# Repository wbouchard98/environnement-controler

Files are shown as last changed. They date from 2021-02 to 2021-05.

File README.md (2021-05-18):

# Projet environnement controlé
Collaborateurs : Simon Jourdenais (Symon4k18) et William Bouchard (wbouchard98)

Ce depôt contient les codes du projet de Serres Domestiques Automatisées, anciennement appelées Environnement Controlé.

Les dossier et fichiers intitulés 'UTest_' sont des tests unitaires.
Le dossier "Trash" contient plusieurs anciens code que nous avons pensés nécessaire, mais après restructuration de notre projet, avons abandonnés. Ces codes ne seront pas aussi bien expliqués et peuvent ne pas toujours fonctionner, mais nous avons décidé de les laisser là comme historique de notre travaille.
Le dossier "Project_Code" contient les codes nécessaires pour faire fonctionner la section logique du projet, tandis que le dossier "Project_EC_GUI" contient les codes nécessaires pour les programmes visuels. Plusieurs version sont disponible montrant l'évolution de notre travaille. Seulement la dernière version est conseillé d'être utilisée.

Le projet suivant sert à prendre des mesures de température, d'humidité et de qualité de l'air, par le biais de différents capteurs et de par la suite
réguler l'environnement.

Voici la liste de matériel utilisé pour le projet:
	1) RaspberryPi 4
	2) PCB "Bloc de capteurs" *
	3) PCB "Bloc de contrôle" *
	4) DS18B20 x2
	5) CSS811
	6) SEN0227
	7) Écran LCD tactile 7 pouces
	8) Bloc d'alimentation d'ordinateur 450 watts

	*Les détails des PCB seront montré plus loin.

Pour que le RaspberryPi fonctionne pour ce projet, voici les étapes que nous avons effectué:

RPIlogo 
# Étapes de l’installation de l’image du Raspberry Pi 

1)	Allez chercher une image de Raspberry Pi Buster Desktop 
2)	”Flash” une carte SD d’au moins 8Go avec cette image. Nous avons utilisé Balena Etcher pour cette étape.
3)	Faire la configuration du Raspberry Pi lors de son premier démarrage. Lorsqu’il vous est demandé de redémarrer le Raspberry Pi, redémarrer le.
4)	Maintenant, il faut activer les interfaces dont on aura besoin. Ouvrez un terminal, et tapez la commande : sudo raspi-config
5)	Une fois la fenêtre de configuration ouverte sélectionner l’index 5(Interfacing Options).
6)	Activer ‘’SSH’’, ‘’VNC’’, ‘’I2C’’ et ‘’1-Wire’’. Il faut aussi activer le ‘’Serial’’. Cependant lorsqu’il va être demandé s’il est désiré que le ‘’login shell’’ soit accessible depuis le serial, faire non, et lorsque l’usager est demandé de vouloir activer le ‘’Serial port hardware’’ faire oui.
7)	Redémarrez le Raspberry Pi pour effectuer les changements.
8)	Maintenant, il faut se connecter au serveur de temps pour pouvoir automatiquement mettre à jour le temps du Raspberry Pi. Ouvrez le fichier /etc/systemd/timesyncd.conf .
9)	Modifiez les lignes ‘’NTP’’ et ‘’FallbackNTP’’ pour que leur valeur sois : time.apple.com .
10)	Effectuez un : sudo systemctl restart systemd-timesync.service .
11)	Effectuer par la suite : sudo systemctl daemon-reload .
12)	Maintenant faire les ‘’update’’ et ‘’upgrade’’.
13)	Si vous utilisez un écran de petite taille, comme un écran 7" comme nous, nous vous recommandons de changer la résolution de l'écran. Pour ce faire, cliquer le logo Raspberry dans le haut de l'écran, puis aller sur "Preferences" et "Raspberry Pi Configuration". Aller dans l'onglet "Display" et puis "Set Resolution...". Nous utilisons "DMT mode 9 800x600 60Hz 4:3".

Une fois le RaspberryPi bien configuré, il faut ajouter les bonnes librairies pythons dans le RaspberryPi pour que les codes puissent bien fonctionner.

Voici les démarches à suivre pour l'installation de ces librairies:

Pyhton
# Étapes pour l’installation des librairies Python

1) Premièrement, il faut s’assurer que Pyhton3 soit bien installé : sudo apt-get install python3 .
2) Une fois installé, il faut pouvoir accéder au I/O du Raspberry Pi. La librairie suivante va faire ce travail : sudo pip3 install RPI.GPIO
3) Pour pouvoir lire les données du capteur SEN0227 qui va lire la température de l’environnement dans lequel le Raspberry Pi se situe (et non l’environnement que l’on souhaite contrôler) : sudo pip3 install sht20 .
4) Maintenant, pour être capable de faire les communications MQTT, il nous faut un "Broker MQTT" : sudo apt-get install mosquitto : et : sudo apt-get install mosquitto-clients .
5) Une fois le "Broker" installé, il nous faut la librairie pour accéder à ce "Broker" : sudo pip3 install paho-mqtt .
6) Maintenant, il faut que notre "GUI" puisse accéder aux librairies PYQT5 : sudo apt-get install qt5-default pyqt5-dev pyqt5-dev-tools
7) Pour contrôler la plupart des éléments de l’environnement, l’utilisation d’un PID est importante. La librairie suivante va nous permettre d’utiliser des PID : sudo pip3 install simple-pid .

Maintenant il est temps d'ajouter les librairies à l'IDE Arduino:

Arduino
# Étape pour l’installation des librairies Arduino

1) Adafruit_CCS811: Pour l'ajouter à l'IDE Arduino, ouvrir l'IDE Arduino, cliquer sur l'onglet "Croquis". Aller par la suite sur "Inclure une bibliothèque" et ensuite "Gérer les bibliothèques". Taper "CCS" dans la barre de recherche et une librairie du nom de "Adafruit CSS811 Library par Adafruit" devrait être disponible. Cliquer sur "Installer".  

2) DFRobot_SHT20: Pour ajouter cette librairie, visiter DFRobot/DFRobot_SHT20 (github.com) . Télécharger le repositary avec le bouton vert avec la flèche. Une fois télécharger mettre le dossier "DFRobot_SHT20-master" dans le dossier "C:\Program Files (x86)\Arduino\libraries". 

3) OneWire: Suivre les étapes pour le Adafruit_CCS811, mais taper "Onewire" dans la barre de recherche. Dans le "ComboBox" "Sujet" sélectionner "Communication". Une librairie du nom de "OneWire" devrait être disponible. Installer celle-ci. 

4) DallasTemperature: Suivre les étapes pour le Adafruit_CCS811, mais tapper "Dallas" dans la barre de recherche. Une librairie du nom de "DallasTemperature" devrait être        disponible. Installer celle-ci. 

## Explication des PCB

Notre projet contient deux PCB. L'un d'entre eux sert à la lecture des capteurs, et l'autre sert à contrôler les diverts éléments de contrôle.
### PCB bloc de capteurs

Pour lire l'état actuel de la chambre, nous avons créé un PCB qui relie plusieurs capteurs(DS18B20, SEN0227, CCS811) à un ATmega328p-AU. Les informations des capteurs sont ensuites transmises au RaspberryPi.
#### Transmission des informations
Nous utilisons la prise USB-mini pour transmettre les informations des capteurs vers le RaspberryPi. Ce même connecteur peut être utilisé pour le transfert du code .ino/.c. Nous avons aussi mis des traces pour un connecteur pour le module bluetooth HM-10.
Pour changer le mode entre Bluetooth et USB, il suffit de changer la position du cavalier JP201 et JP203 (position 1-2 Bluetooth, 2-3 USB). 
Dans notre projet nous utilisons pas le module Bluetooth, alors aucun code n'a été fait pour son utilisation, mais son ajout peut être possible grâce au PCB.
#### Alimentation
L'alimentation de ce PCB vient du câble USB, mais si on désire utiliser le module Bluetooth, alors un connecteur(J202) permet de connecter une batterie Li-po de 5V pour alimenter le montage de façon indépendante au RaspberryPi.
Comme mentionné plus tôt, nous utilisons la communication USB, alors l'alimentation provenant de batterie Li-po n'a pas été testé.
#### Communication des capteurs
##### DS18B20
Le capteur de température DS18B20 communique avec le ATmega en protocole 1-wire. La plaque contient une empreinte pour placer directement un DS18B20 en format TO-92, et un connecteur permet de pouvoir aussi utiliser un DS18B20.
##### SEN0227
Le capteur de température/humidité SEN0227 communique en I2C avec le ATmega. La plaque contient une empreinte pour placer directement un SHT-20, et un connecteur permet de pouvoir aussi utiliser un SEN0227.
##### CCS811
Le capteur de qualité de l'air CCS811 communique en I2C avec le ATmega. La plaque contient les empreintes pour placer directement CCS811 et les composants requis pour son fonctionement, et un connecteur permet de pouvoir aussi utiliser un CCS811 de Keyestudio.
La trace JP301 permet de changer l'adresse du CCS811.
##### SGP30
Le capteur de qualité de l'air SGP30 communique en I2C avec le Atmega. La plaque contient une empreinte pour placer directement un SGP30, et un connecteur permet de pouvoir aussi utiliser un "board" SGP30 de Adafruit.
Dans notre projet nous utilisons pas le SGP30, alors aucun code dans notre conteneur Github sera fait avec la considération de son utilisation, mais il sera possible de modifier le code pour l'inclure s'il est désiré.

### PCB de contrôle

Ce PCB sert à transformer les PWM du RaspberryPi, pour qu'ils soient capable de contrôler les éléments de contrôle(Lumière, ventillation, chauffage, humidificateur).

#### Connection au RaspberryPi
Le RaspberryPi se connecte au PCB par l'entremise d'un câble plat 40 pins.
#### Ventillation
La ventillation est contrôllé par le GPIO-27 du RaspberryPi. Le signal du GPIO-27 est ensuite transformer en 120 VAC par un CPC1966B pour faire fonctionner le système de ventillation.

#### Élément chauffant
Même méthode que pour la ventillation, mais le GPIO-17 est utilisé.

#### Lumière
Même principle que la ventillation, mais le GPIO-06 est utilisé.

#### Déshumidificateur
Même principle que la ventillation, mais le GPIO-22 est utilisé. On a pas intégré le déshumidificateur à notre projet, alors notre code ne contient pas son activation, mais il est possible d'ajouter son activation si désiré.

#### Humidificateur
L'humidificateur est contrôlé par le GPIO-05 du RaspberryPi. Un CPC1907B transforme le signal du RaspberryPi en signal 24V.

#### LED 100W
Une LED de 100W peut être connecté au PCB pour utiliser au lieu du panneau de lumière. Cette lumière sera contrôlé par le GPIO-13 du RaspberryPi. Un transitor permet de faire circuler le courant pour allumer la LED.

#### Ventillation du boitier
Un ventillateur à l'intérieur du boitier permet de refroidir la température de celui-ci. Ce ventillateur est contrôllé par un PWM de la pin GPIO-12 du RaspberryPi. Un transitor permet de conduire le courant à partir du 12V.

#### Ventillateur de la LED 100W
Un ventillateur qui permet de refroidir la LED de 100W. Ce ventillateur est "driver" par un transitor contrôlé par la pin GPIO-18 du RaspberryPi.

#### Connecteur 12V supplémentaire
On ajouté ce connecteur pour pouvoir ajouter d'autre élément fonctionnant sur du 12V. Comme par exemple une pompe à eau pour arroser la terre ou un ventillaeur supplémentaire. Ce connecteur sera contrôler par la pin GPIO-19 du RaspberryPi.

## Utilisation de l'interface graphique
L'interface graphique se compose de deux sections: un menu ancré sur la gauche de l'écran et l'affichage principale qui occupe le restant. Voir figure ci-dessus.

SecGUI

Le menu nous permet de naviguer entre 4 modes de GUI différents. Le premier est le mode monitorage, le deuxième est le mode consigne, le troisième est le mode paramètre et finalement le dernier est le mode administrateur.

### Mode Monitorage
Le mode monitorage est bien simple; il affiche les valeurs reçues. Les valeurs sont la température, l'humidité, la concentration de C02 et la quantité de matière organique dans l'air. Voir la figure ci-dessus pour exemple de l'affichage en mode monitorage.

MonGUI

### Mode Consigne
Le mode consigne permet à l'usager d'accomplir plusieurs tâches. Premièrement, une section de l'affichage est réservé à afficher les valeurs de consignes courantes. Une autre section sert à modifier manuellement les valeurs des consignes courantes. Les valeurs à l'écran dans la section de l'affichage des consignes vont changer avec les modifications effectué. L'autre section sert à choisir ou enregistrer des valeurs de consignes. Ces valeurs sont alors réutilisables si l'usager souhaite les utiliser plus tard, ou si le système est mis hors tension. Voir la figure ci-dessus pour un visuel du GUI en mode consigne. Il est aussi possible d'ouvrir une autre fenêtre qui va permettre le contrôle des lumières.

ConGUI

#### Mode éclairage
Appelé à partir de la fenêtre consigne, permet de configurer un cycle d'activation et de désactivation des lumières.

ConGUI

### Mode Paramètre
Le mode paramètre nous permet de se connecter à la base de données ThingSpeak, de se connecter à un réseau Wi-Fi et à voir des informations utiles pour l'usgaer. Pour pouvoir entrer les informations requises de Thingspeak et du Wi-Fi, un clavier sera nécessaire. Simplement le brancher dans un port USB du RaspberryPi. L'iamge ci-dessous nous permet de voir un exemple de la fenêtre paramètre.

ParaGUI

### Mode Administrateur
Le mode Administarteur permet de contrôler manuellement les éléments de contrôle. Cette fenêtre est très utile pour vérifier le fonctionnment de son matériel. Des "sliders" servent à ajuster le PWM des éléments et ainsi dicter leur intensité de fonctionnment. Voir la figure ci-dessus pour un apperçu.

AdminGUI

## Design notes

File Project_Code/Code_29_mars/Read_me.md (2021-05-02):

# Fonctionnement des codes du projet

Les programmes dans ce dossier sont les programmes les plus à jours à date du 29 Mars 2021. Ces programmes peuvent fonctioner à l'aide du PCB "Bloc de capteur" ou à l'aide d'un Arduino Nano
avec les capteurs relié au bonne pattes de communication.

Pour pouvoir avoir les librairies nécessaire et que la configuration des systèmes soient correct, veuillez vous référer au Read_me.md principal du répertoire GitHub.

## P_p_3.py

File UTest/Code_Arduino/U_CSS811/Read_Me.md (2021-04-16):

Test unitaire pour le fonctionnement du capteur CCS811. 
IMPORTANT!!!!!! Le capteur de CO2 nécessite 48H de marche, après chaque mise a l'arrêt avant de donner des donées précises.
Pour vérifier son fonctionnement, veuillez le connecter au RaspberryPi et mettre en marche le code Userial_read_from_arduino.py dans le RaspberryPi.

Matériel:
	ARDUINO NANO
	CONVERTISSEUR 5v -> 3.3V
	RASPBERRY PI 3B
	CAPTEUR CCS811

Connexion:
	Pour que le test du capteur CCS811 fonctionne, les connexions suivantes doivent être éffectuées:

		ARDUINO NANO -> CC811:
			GND  ->  GND
			5V   ->  VCC
			A4   ->  SDA
			A5   ->  SCL
			GND  ->  WAKE
			N.C. ->  RST, INT

		ARDUINO NANO -> CONVERTISSEUR(HIGH/LOW) -> RASPBERRY PI 3B
			GND  ->  	GND <-> GND    	<-  GND		#Connection du GND entre le RPi et le ARDUINO direct + connexion au GND du convertisseur
			5V   ->		HV  :  LV       <-  3.3V
			RX0  ->         HV3 :  LV3      <-  TX(Pin8)
			TX1  ->         HV1 :  LV1      <-  RX(Pin10)

Prérequis:
	Programme Arduino:
		Pour le bon fonctionnement du programme Arduino, la librairie "Adafruit_CCS811" est nécessaire.
		Pour l'installer dans l'IDE ARDUINO:
			1) Ouvrir l'IDE ARDUINO
			2) Cliquer sur 'Croquis' dans la barre d'outils.
			3) Sélectionner 'Inclure une bibliothèque', puis 'Gérer les bibliothèque'.
			4) Dans la nouvelle fenêtre, assurez-vous que 'Type' et 'Sujet' sois a 'Tout'.
			5) Dans le filtre de recherche, tapez 'CCS811' et une librairie Adafruit devrait être disponible. Cliquer sur 'Installer'.
			6) Redémarrez l'IDE.

Transfert du code ARDUINO (CCS881.c):
	1) Assurez-vous que les options de téleversement soient les bonnes. (Carte: "Arduino Duemilanove", Processeur: "ATmega328p", PORT: Choisir le bon, Programmateur: "AVR ISP")
	2) Avant de téléverser le code, débrancher les connections rx/tx du ARDUINO NANO pour que le port série communique bien avec celui de l'ordinateur.
	3) Une fois le code téléverser, refaire les connections RX/TX.

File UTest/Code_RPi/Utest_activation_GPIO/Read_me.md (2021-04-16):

Test unitaire pour tester la librairie RPi.GPIO.

Le test sert à savoir si les librairies de base python ont bien été installées. (Pour installer python: sudo apt-get install pyhton3)

Le script met un état haut au GPIO-16 du Pi pendant 5 secondes.

Matériel:

	RASPBERRY PI 3B

PRÉALLABLES :

	Vous deves avoir la librairie RPi.GPIO. Pour l'installée, entrer la commande suivante dans un terminal: sudo pip3 install RPi.GPIO

EXÉCUTION : 

	Excécuter le programme et vérifier l'état du GPIO-16 du RaspberryPi. Si un état haut de 5 secondes est détecté, alors la librairie devrait être OK.

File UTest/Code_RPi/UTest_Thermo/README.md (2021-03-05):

README pour le fichier UTest_Thermo_DS18B20.py

BRANCHEMENT :

Le thermomêtre DS18B20 doit être alimenté avec 5 volts ou 3.3 Volts et le brancher sur l'entrée IO4, qui corresponds à la pin 1-Wire.
Ne pas oublier d'ajouter une pull-up de 4.7k sur le one-wire

PRÉALLABLES :

Pour exécuter ce programme de test unitaire, vous devez préallablement configurer votre Raspberry Pi. 
Exécuter la commande 'sudo raspi-config', puis dans la section 'Interfaces', activez l'interface '1-Wire'.

De plus, exécutez la ligne 'sudo pip3 install w1thermsensor' pour installer la librairie du thermomêtre dans le dossier contenant ce fichier.

EXÉCUTION : 

Une fois fait, ouvrez un terminal dans le dossier UTest_Thermo et exécutez la ligne 'python UTest_Thermo_DS18B20.py'.
La valeur lue du thermomêtre sera alors affichée dans le terminal si tout est bien branché et que les préallables on été faits et/ou installés.

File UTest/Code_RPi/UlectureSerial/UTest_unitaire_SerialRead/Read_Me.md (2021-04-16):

Test unitaire pour la lecture du port série.
Le faire marcher avec le code CCS811.c du Arduino Nano permet de vérifier si la communication série est bien établie et si le capteur CCS811 est fonctionnel.
Permet aussi de s'assurer que la configuration du port série du Raspberry Pi à bien été faite.

Matériel:
	ARDUINO NANO
	CONVERTISSEUR 5v -> 3.3V
	RASPBERRY PI 3B

Connexion:

		ARDUINO NANO -> CONVERTISSEUR(HIGH/LOW) -> RASPBERRY PI 3B
			GND  ->  	GND <-> GND    	<-  GND		#Connection du GND entre le RPi et le ARDUINO direct + connexion au GND du convertisseur
			5V   ->		HV  :  LV       <-  3.3V
			RX0  ->         HV3 :  LV3      <-  TX(Pin8)
			TX1  ->         HV1 :  LV1      <-  RX(Pin10)

Le programme suivant devrait lire ce qui est sur le port série et afficher le résultat en console.

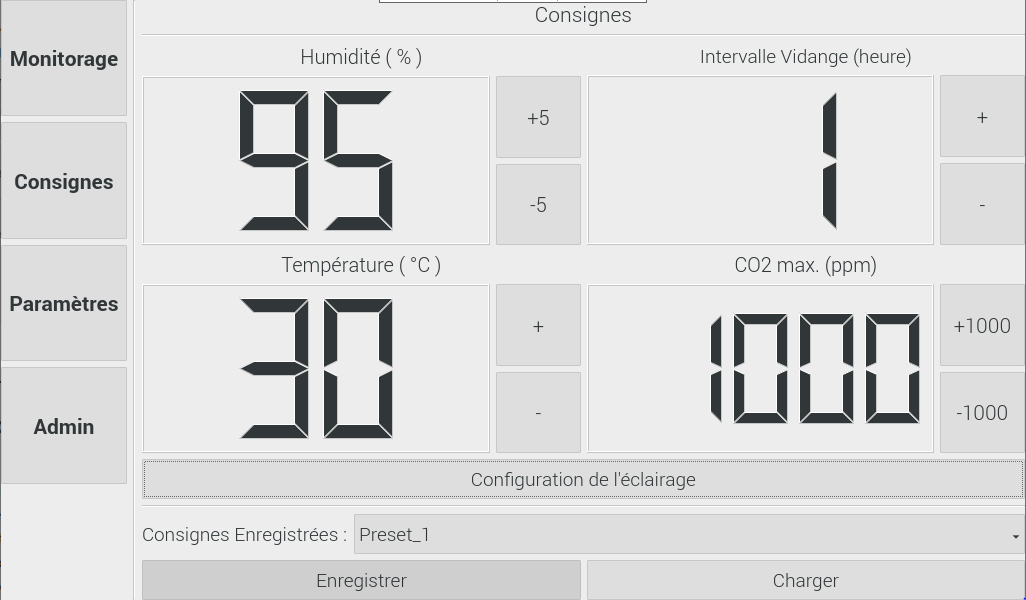
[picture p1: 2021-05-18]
Trash/CaptureControl.PNG

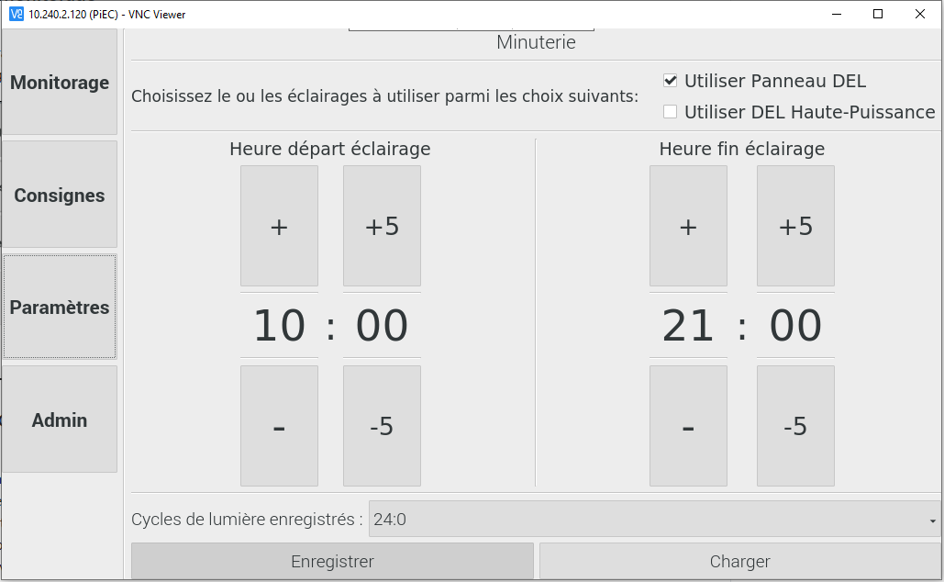
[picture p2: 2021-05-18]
Trash/CaptureControlTime.PNG

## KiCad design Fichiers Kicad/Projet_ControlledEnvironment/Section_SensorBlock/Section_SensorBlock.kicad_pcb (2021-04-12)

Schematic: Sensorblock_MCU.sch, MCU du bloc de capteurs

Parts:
C201, C202, C205, C206, C208: 0.1 uF; C_0805_2012Metric
C203, C204: 18 pF; C_0805_2012Metric
C207: 1 uF; C_0805_2012Metric
C209: 10 uF; C_0805_2012Metric
D201: D_Schottky; D_0805_2012Metric
D202: LED_RED_TX; LED_0805_2012Metric
D203: LED_BLUE_RX; LED_0805_2012Metric
D205: LED_YLW_USR; LED_0805_2012Metric
D206: LED_RED; LED_0805_2012Metric
D207, D208: LED_YLW; LED_0805_2012Metric
D209, D210: LED_GRN; LED_0805_2012Metric
ICSP201: Conn_02x03; PinHeader_2x03_P2.54mm_Vertical
J201: USB_B_Mini; USB_Mini-B_Lumberg_2486_01_Horizontal
J202: Conn_01x02_Female; PinSocket_1x02_P2.54mm_Vertical
J203: Sense_Batt; PinSocket_1x01_P2.54mm_Vertical
JP201, JP203: Jumper_NC_Dual; PinHeader_1x03_P2.54mm_Vertical
R201: 90k; R_0805_2012Metric
R202, R203: 10k; R_0805_2012Metric
R204, R205, R208, R209, R210, R211, R212, R213: 330; R_0805_2012Metric
R206: 4.7k; R_0805_2012Metric
SW201: Reset; SW_SPST_CK_RS282G05A3
SW202: SW_Push; SW_PUSH-12mm_Wuerth-430476085716
U201: ATmega328P-AU; TQFP-32_7x7mm_P0.8mm
U202: FT232RL; SSOP-28_5.3x10.2mm_P0.65mm
U203: HM10; PinHeader_1x04_P2.54mm_Vertical
U204: AP2210-3.3; SOT-23
Y201: 16 MHz; Crystal_SMD_5032-2Pin_5.0x3.2mm

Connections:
+3V3: C208.1, C209.1, U202.17, U204.2; also elsewhere on the board
+5V: C201.2, C202.2, C205.2, C207.1, D201.1, ICSP201.2, J202.1, R203.1, R204.2, R205.1, SW202.1, U201.4 (VCC), U201.6 (VCC), U201.18 (AVCC), U202.4, U202.20, U203.4, U204.3; also elsewhere on the board
/Sensorblock MCU sheet/BTN_In: R206.1, SW202.2, U201.23 (PC0)
/Sensorblock MCU sheet/BT_RX: JP201.1, U203.1
/Sensorblock MCU sheet/BT_TX: JP203.1, U203.2
/Sensorblock MCU sheet/DTR: C206.1, U202.2
/Sensorblock MCU sheet/LED_Meter_1: D206.2, U201.1 (PD3)
/Sensorblock MCU sheet/LED_Meter_2: D207.2, U201.2 (PD4)
/Sensorblock MCU sheet/LED_Meter_3: D208.2, U201.9 (PD5)
/Sensorblock MCU sheet/LED_Meter_4: D209.2, U201.10 (PD6)
/Sensorblock MCU sheet/LED_Meter_5: D210.2, U201.11 (PD7)
/Sensorblock MCU sheet/PB2-SS: U201.14 (PB2)
/Sensorblock MCU sheet/PB3-MOSI: ICSP201.4, U201.15 (PB3)
/Sensorblock MCU sheet/PB4-MISO: ICSP201.1, U201.16 (PB4)
/Sensorblock MCU sheet/PB5-SCK: D205.2, ICSP201.3, U201.17 (PB5)
/Sensorblock MCU sheet/PC6-RST: C206.2, ICSP201.5, R203.2, SW201.1, U201.29 (~RESET~/PC6)
/Sensorblock MCU sheet/RX_ARD: JP203.2, U201.30 (PD0)
/Sensorblock MCU sheet/TX_ARD: JP201.2, U201.31 (PD1)
/Sensorblock MCU sheet/USB_RX: JP201.3, U202.5
/Sensorblock MCU sheet/USB_TX: JP203.3, U202.1
AT_1Wire: U201.32 (PD2); also elsewhere on the board
AT_SCL: U201.28 (PC5); also elsewhere on the board
AT_SDA: U201.27 (PC4); also elsewhere on the board
unnamed: C203.2, U201.7 (XTAL1/PB6), Y201.1
unnamed: C204.2, U201.8 (XTAL2/PB7), Y201.2
unnamed: D201.2, J201.1 (VBUS)
unnamed: D202.1, U202.23
unnamed: D202.2, R204.1
unnamed: D203.1, U202.22
unnamed: D203.2, R205.2
unnamed: D205.1, R208.1
unnamed: D206.1, R209.1
unnamed: D207.1, R210.1
unnamed: D208.1, R211.1
unnamed: D209.1, R212.1
unnamed: D210.1, R213.1
unnamed: J201.2 (D-), U202.16
unnamed: J201.3 (D+), U202.15
unnamed: J203.1, R201.1
unnamed: R201.2, R202.1, U201.24 (PC1)

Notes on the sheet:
Pour entrée 5V de batterie LiPo
Si le module Bluetooth est utilisé, ne pas oublier de changer les cavaliers de position!
Régulateur 3.3 pour les capteurs - Le FTDI ne peux sourcer plus de 50 mA

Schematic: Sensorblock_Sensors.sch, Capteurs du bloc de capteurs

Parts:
C301, C302: 0.1 uF; C_0805_2012Metric
J301: Conn_OLED_Screen; PinSocket_1x04_P2.54mm_Vertical
J302: Conn_01x04; PinSocket_1x04_P2.54mm_Vertical
J303: Conn_QT_CCS; PinSocket_1x04_P2.54mm_Vertical
J304: Conn_Keyes_CCS; PinSocket_1x07_P2.54mm_Vertical
J305: Conn_QT_SGP30; PinSocket_1x04_P2.54mm_Vertical
J306: Conn_01x03; PinSocket_1x03_P2.54mm_Vertical
JP301: Jumper_Address_I2C; SolderJumper-2_P1.3mm_Open_TrianglePad1.0x1.5mm
Q301, Q302, Q303: BSS138; SOT-23
R301, R302, R303, R304, R305, R306, R307, R309: 10k; R_0805_2012Metric
R311: 4.7 Ohms; R_0603_1608Metric
R312: 100k; R_0805_2012Metric
TH301: 10k; R_0402_1005Metric
U301: CCS811; AMS_LGA-10-1EP_2.7x4mm_P0.6mm
U302: DS18B20; TO-92_Inline
U303: SHT2x; DFN-6-1EP_3x3mm_P1mm_EP1.5x2.4mm
U304: SGP30; DFN-7

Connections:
+3V3: C301.1, J301.3, J302.2, J303.2, J304.2, J305.2, J306.1, JP301.1, Q301.1, Q302.1, Q303.1, R304.2, R305.2, R306.2, R309.2, R311.1, R312.2, U301.2, U301.6, U302.3 (VDD), U303.5, U304.5; also elsewhere on the board
+5V: R301.2, R302.2, R303.2; also elsewhere on the board
/Sensorblock sensor sheet/1Wire_3V3: J306.2, Q303.2, R306.1, U302.2 (DQ)
/Sensorblock sensor sheet/CO2_!Int: U301.3
/Sensorblock sensor sheet/SCL_3V3: J301.2, J302.4, J303.4, J304.4, J305.4, Q301.2, R304.1, U301.10, U303.6, U304.6
/Sensorblock sensor sheet/SDA_3V3: J301.1, J302.3, J303.3, J304.3, J305.3, Q302.2, R305.1, U301.9, U303.1, U304.3
AT_1Wire: Q303.3, R303.1; also elsewhere on the board
AT_SCL: Q301.3, R301.1; also elsewhere on the board
AT_SDA: Q302.3, R302.1; also elsewhere on the board
unnamed: C302.2, R311.2, U304.1
unnamed: JP301.2, R307.2, U301.1
unnamed: R312.1, TH301.2, U301.8
unnamed: TH301.1, U301.4, U301.5

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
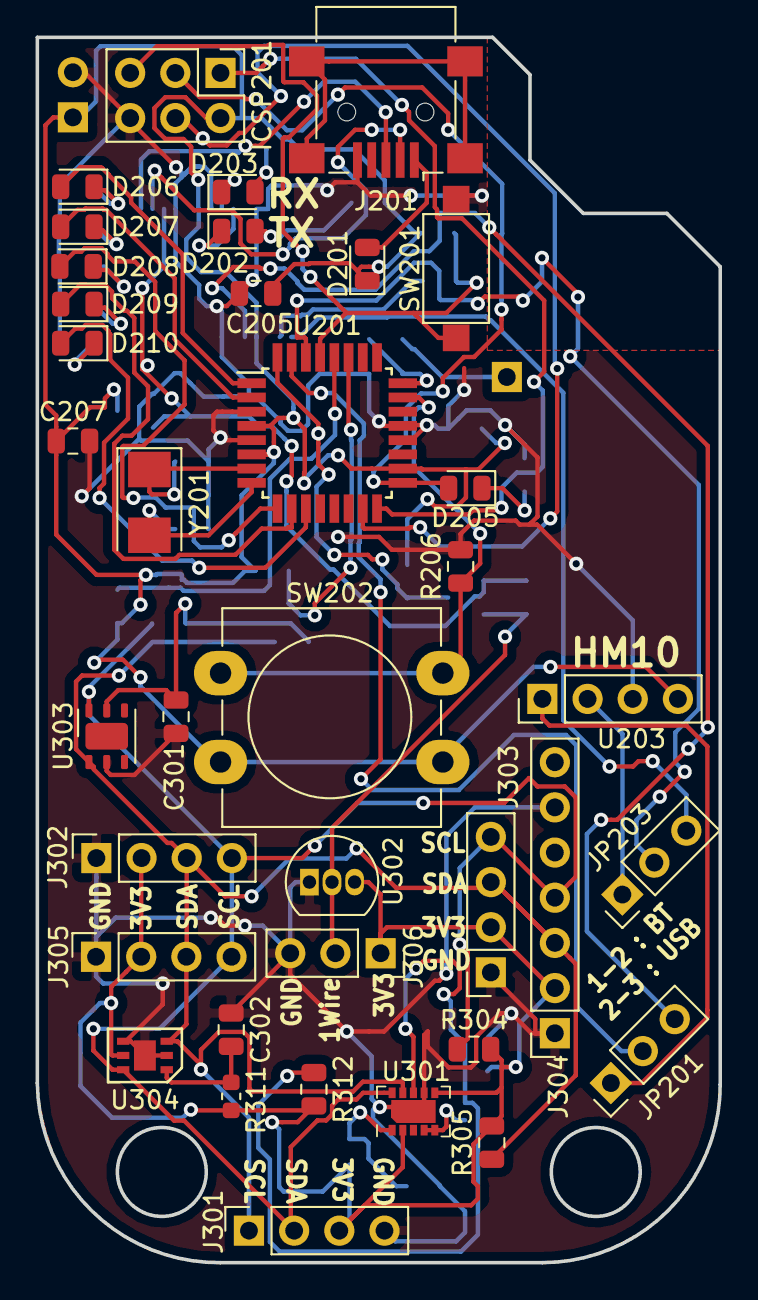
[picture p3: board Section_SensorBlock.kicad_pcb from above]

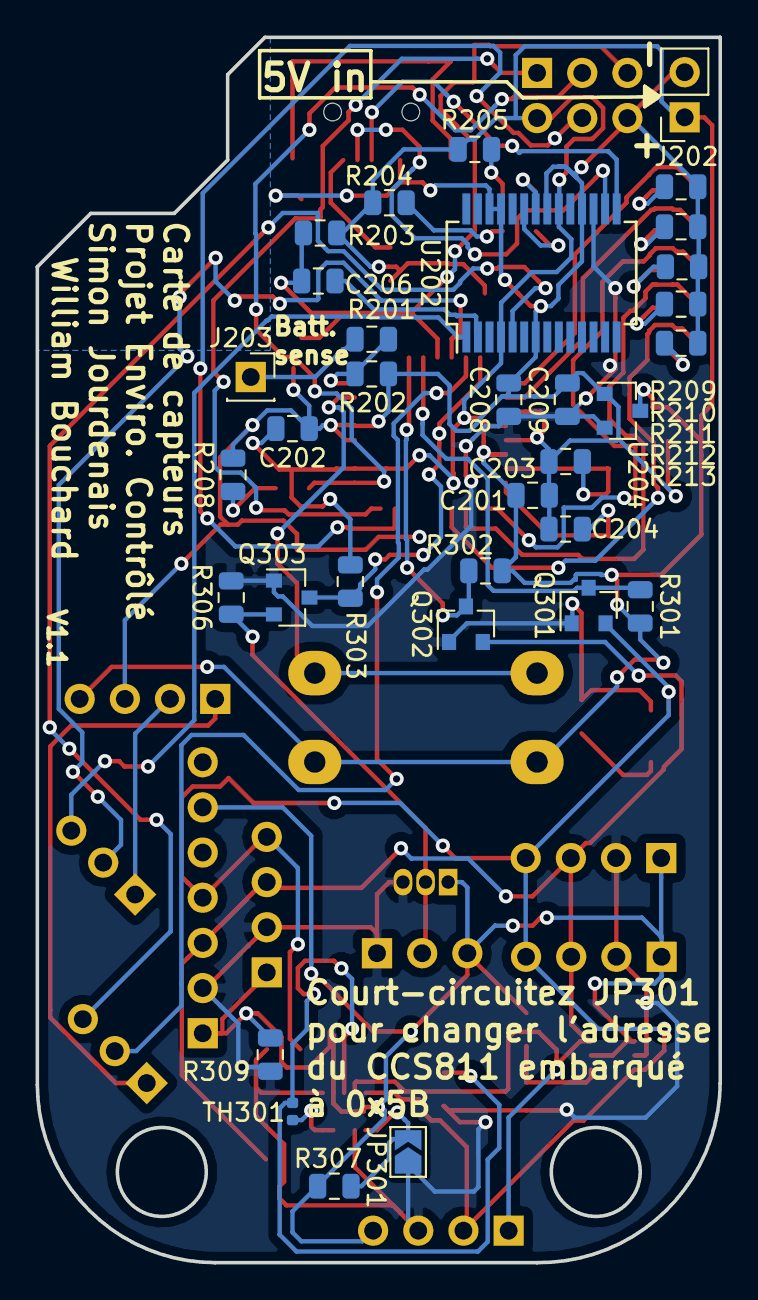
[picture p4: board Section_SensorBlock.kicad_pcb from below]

Board: 2 copper layers, 38.4 x 68.9 mm, 70 parts (33 on the bottom side), 47 nets.

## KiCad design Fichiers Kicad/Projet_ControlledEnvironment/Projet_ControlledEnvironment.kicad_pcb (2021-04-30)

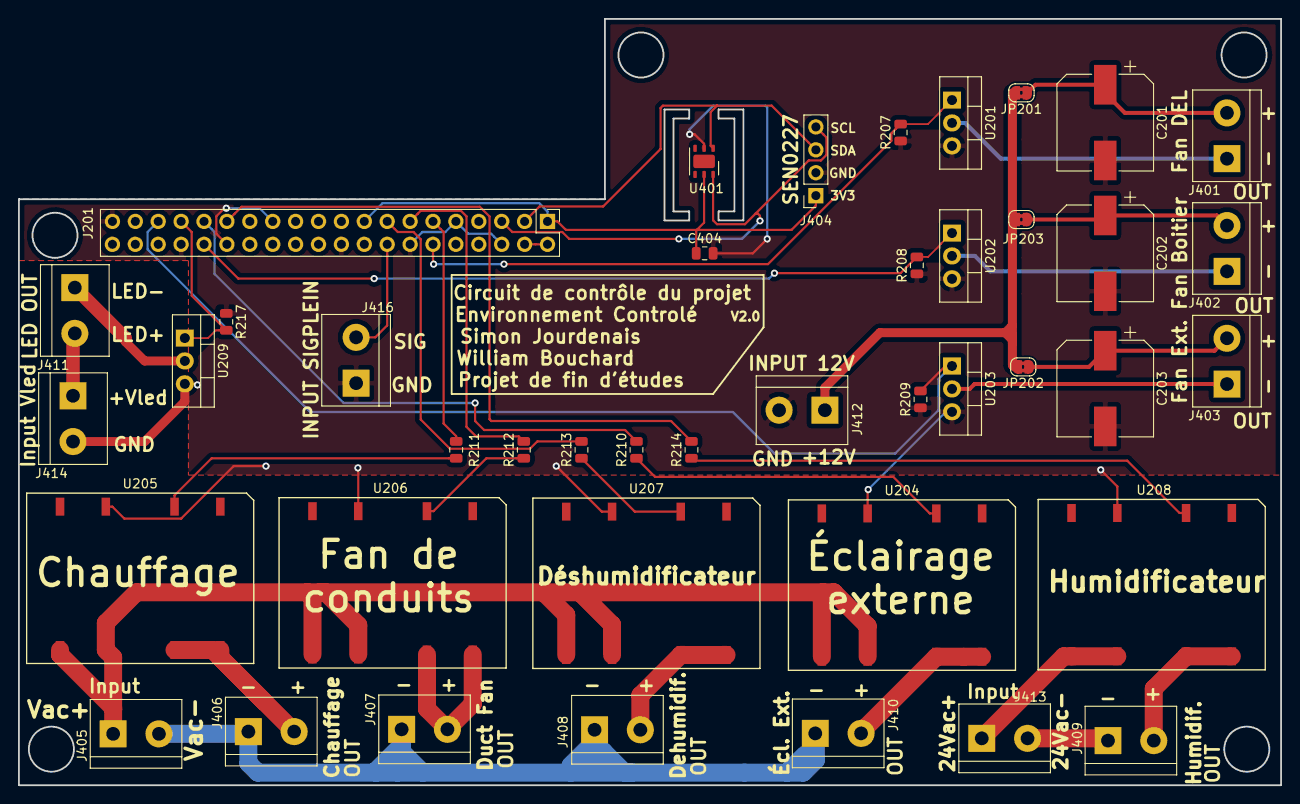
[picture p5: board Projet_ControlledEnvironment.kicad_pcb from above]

Board: 2 copper layers, 140.0 x 85.0 mm, 42 parts (0 on the bottom side), 38 nets.

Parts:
C201, C202, C203: 470 uF; CP_Elec_10x10.5
C404: 0.1 uF; C_0805_2012Metric
J201: Pi 40-Pin Connector; PinHeader_2x20_P2.54mm_Vertical
J401, J402, J403, J405, J406, J407, J408, J409, J410, J411, J412, J413, J414, J416: Conn_01x02; TerminalBlock_bornier-2_P5.08mm
J404: Conn_01x04; PinSocket_1x04_P2.54mm_Vertical
JP201, JP202, JP203: SolderJumper_2_Bridged; SolderJumper-2_P1.3mm_Bridged2Bar_RoundedPad1.0x1.5mm
R207, R208, R209, R217: 10k; R_0805_2012Metric
R210, R211, R212, R213, R214: 420; R_0805_2012Metric
U201, U202, U203, U209: FQP30N06L; TO-220-3_Vertical
U204, U205, U206, U207: CPC1966B; PSOIC-8
U208: CPC1907B; PSOIC-8
U401: SHT2x; DFN-6-1EP_3x3mm_P1mm_EP1.5x2.4mm

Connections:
24VAC+: J413.1, U208.5, U208.6
24VAC-: J409.1, J413.2
100W_LED+: J411.2, J414.1
100W_LED-: J411.1, U209.2
+3V3: C404.1, J201.1, J201.17, J404.1, U401.5
+5V: J201.2, J201.4
+12V: J412.1, JP201.2, JP202.2, JP203.2
/Mainblock Core/GPIO5: J201.29, R214.2
/Mainblock Core/GPIO6: J201.31, R210.2
/Mainblock Core/GPIO12: J201.32, R208.2, U202.1
/Mainblock Core/GPIO13: J201.33, R217.2, U209.1
/Mainblock Core/GPIO17: J201.11, R211.2
/Mainblock Core/GPIO18: J201.12, R207.2, U201.1
/Mainblock Core/GPIO19: J201.35, R209.2, U203.1
/Mainblock Core/GPIO22: J201.15, R213.2
/Mainblock Core/GPIO27: J201.13, R212.2
BOITIER_FAN_IN: C202.1, J402.2, JP203.1
BOITIER_FAN_OUT: J402.1, U202.2
Dehumidificateur: J408.2, U207.7, U207.8
DuctFan: J407.2, U206.7, U206.8
EXT_OPT_FAN_IN: C203.1, J403.2, JP202.1
EXT_OPT_FAN_OUT: J403.1, U203.2
Ext_Light: J410.2, U204.7, U204.8
GND: C201.2, C202.2, C203.2, C404.2, J201.6, J201.9, J201.14, J201.20, J201.25, J201.30, J201.34, J201.39, J404.2, J412.2, J414.2, J416.1, R207.1, R208.1, R209.1, R217.1, U201.3, U202.3, U203.3, U204.3, U205.3, U206.3, U207.3, U208.3, U209.3, U401.2
GPIO23_SIGPLEIN: J201.16, J416.2
Heater: J406.2, U205.7, U205.8
Humidificateur: J409.2, U208.7, U208.8
LED_FAN_IN: C201.1, J401.2, JP201.1
LED_FAN_OUT: J401.1, U201.2
unnamed: R210.1, U204.2
unnamed: R211.1, U205.2
unnamed: R212.1, U206.2
unnamed: R213.1, U207.2
unnamed: R214.1, U208.2
SCL_PI: J201.5, J404.4, U401.6
SDA_PI: J201.3, J404.3, U401.1
VAC+: J405.1, U204.5, U204.6, U205.5, U205.6, U206.5, U206.6, U207.5, U207.6
VAC-: J405.2, J406.1, J407.1, J408.1, J410.1

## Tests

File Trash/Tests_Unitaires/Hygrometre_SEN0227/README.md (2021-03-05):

README pour le fichier UTest_Hygro_SEN0227.py

BRANCHEMENT :

L'hygromètre SEN0227 doit être alimenté avec 3.3 Volts, son 'SDA' branché dans l'entrée IO2 et le 'SCL' dans l'entrée IO3.

PRÉALLABLES :

Pour executer ce programme de test unitaire, vous devez préallablement configurer votre Raspberry Pi. 
Éxecuter la commande 'sudo raspi-config', puis dans la section 'Interfaces', activez l'interface 'I2C'.

De plus, executez la ligne 'sudo pip3 install sht20' pour installer la librairie du capteur.

EXÉCUTION : 

Une fois fait, ouvrez un terminal dans le dossier UTest_Hygro et exécutez la ligne 'python UTest_Hygro_SEN0227.py'.
Les valeurs lues du capteur seront alors affichées dans le terminal si tout est bien branché et que les préallables on été faits et/ou installés.

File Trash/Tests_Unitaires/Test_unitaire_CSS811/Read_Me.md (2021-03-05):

Test unitaire pour le fonctionnement du capteur CCS811. 
IMPORTANT!!!!!! Le capteur de CO2 nécessite 48H de marche, après chaque mise a l'arrêt avant de donner des donées précises.

Matériel:
	ARDUINO NANO
	CONVERTISSEUR 5v -> 3.3V
	RASPBERRY PI 3B
	CAPTEUR CCS811

Connexion:
	Pour que le test du capteur CCS811 fonctionne, les connexions suivantes doivent être éffectuées:

		ARDUINO NANO -> CC811:
			GND  ->  GND
			5V   ->  VCC
			A4   ->  SDA
			A5   ->  SCL
			GND  ->  WAKE
			N.C. ->  RST, INT

		ARDUINO NANO -> CONVERTISSEUR(HIGH/LOW) -> RASPBERRY PI 3B
			GND  ->  	GND <-> GND    	<-  GND		#Connection du GND entre le RPi et le ARDUINO direct + connexion au GND du convertisseur
			5V   ->		HV  :  LV       <-  3.3V
			RX0  ->         HV3 :  LV3      <-  TX(Pin8)
			TX1  ->         HV1 :  LV1      <-  RX(Pin10)

Prérequis:
	Programme Arduino:
		Pour le bon fonctionnement du programme Arduino, la librairie "Adafruit_CCS811" est nécessaire.
		Pour l'installer dans l'IDE ARDUINO:
			1) Ouvrir l'IDE ARDUINO
			2) Cliquer sur 'Croquis' dans la barre d'outils.
			3) Sélectionner 'Inclure une bibliothèque', puis 'Gérer les bibliothèque'.
			4) Dans la nouvelle fenêtre, assurez-vous que 'Type' et 'Sujet' sois a 'Tout'.
			5) Dans le filtre de recherche, tapez 'CCS811' et une librairie Adafruit devrait être disponible. Cliquer sur 'Installer'.
			6) Redémarrez l'IDE.

Transfert du code ARDUINO (CCS881.c):
	1) Assurez-vous que les options de téleversement soient les bonnes. (Carte: "Arduino Duemilanove", Processeur: "ATmega328p", PORT: Choisir le bon, Programmateur: "AVR ISP")
	2) Avant de téléverser le code, débrancher les connections rx/tx du ARDUINO NANO pour que le port série communique bien avec celui de l'ordinateur.
	3) Une fois le code téléverser, refaire les connections RX/TX.

Démarrage du code du RASPBERRY PI (serial_read_from_arduino.py):
	1) Une fois le transfert du code ARDUINO fait, simplement ouvrir l'IDE Thonny et partir le programme python.
	2) Les messages devraient s'afficher dans le terminal.

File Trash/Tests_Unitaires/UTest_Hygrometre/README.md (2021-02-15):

README pour le fichier UTest_Hygro_SEN0227.py

BRANCHEMENT :

L'hygrometre SEN0227 doit etre alimente avec 3.3 Volts, son 'SDA' branche dans l'entree IO2 et le 'SCL' dans l'entree IO3.

PREALLABLES :

Pour executer ce programme de test unitaire vous devez preallablement configurer votre Raspberry Pi. 
Executer la commande 'sudo raspi-config', puis dans la section 'Interfaces', activez l'interface 'I2C'.

De plus, executez la ligne 'sudo pip3 install sht20' pour installer la librairie du capteur.

EXECUTION : 

Une fois fait, ouvrez un terminal dans le dossier UTest_Hygro et executez la ligne 'python UTest_Hygro_SEN0227.py'.
Les valeur lues du capteur seront alors affichees dans le terminal si tout est bien branche et que les preallables on ete faits et/ou installes.

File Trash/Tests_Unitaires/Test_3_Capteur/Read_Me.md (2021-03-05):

Test de lecture du capteur DS18B20, SEN0227 et CCS811 dans le même exécutable python.
Pour le bon branchement et fonctionnement des capteurs, veuillez-vous référer au Read_Me.md correspondant à chacun des tests unitaires.

	Pour le capteur CCS811, allez voir le fichier "Read_Me.md" du repertoire "Tests_Unitaires/Test_unitaire_CSS811".
	Pour le capteur DS18B20, allez voir le fichier "README.md" du repertoire "Tests_Unitaires/UTest_Thermo".
	Pour le capteur SEN0277, allez voir le fichier "README.md" du repertoire "Tests_Unitaires/Hygrometre_SEN0227".

Avant de faire fonctionner ce programme, il ne faut pas oublier de bien avoir mis le programme dans le ARDUINO NANO et de bien faire les connections.

Prérequis:
	En plus des prérequis des autres Read_me.md, il faut que l'installation et la configuration de InfluxDB sois fait.
	Veuillez-vous référer à ce site pour la démarche à suivre: https://pimylifeup.com/raspberry-pi-influxdb/
	
	Il faut aussi faire: sudo pip3 install influxdb

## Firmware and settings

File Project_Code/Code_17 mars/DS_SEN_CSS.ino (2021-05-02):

#include <OneWire.h> 
#include <Wire.h>
#include <DallasTemperature.h>
//#include <PID_v1.h>
#include <Adafruit_CCS811.h>
#include <DFRobot_SHT20.h>
//#include "Adafruit_seesaw.h"



//#define HEATCABLE 3
#define ONE_WIRE_BUS 2 
#define UPDATE_DELAY_MS 1000

//void readCableTemp();
void readCCS();
void readSHT20();
//void setPIDOutput();
void initCCS811();
void initSHT20();
void readDS18B20();
//float mapFloatToPercent(float var, float inLow, float inHigh);

/*const char * states[]= 
{
  "OFF",
  "MAINTAIN",
  "HEATING"
};*/

/*enum stateEnums 
{
  OFF=0,
  MAINTAIN,
  HEATING
};*/

unsigned long pastTime = 0; //last time the sensor was triggered
unsigned long currentTime = millis();

//Vars pour PID
/*stateEnums state_PID = OFF;
double currentTemp; 
double PIDOut = 0;
double difference = 6;
double setPoint = 30;
int Kp = 10;
int Ki = 5;
int Kd = 2;
*/
//Vars pour le capteur Keyestudio CCS811 (Adafruit 3566 https://www.adafruit.com/product/3566)
int ppm_Dioxide=-1;
int ppb_TVOC=-1;

//Vars pour le capteur DFRobot SEN0227//SHT20
float temp_SEN, humid_SEN, tempDS;

//Vars pour le capteur Adafruit Stemma Soil Sensor  (Adafruit 4026 https://www.adafruit.com/product/4026)
//float temp_GND, humid_GND;

Adafruit_CCS811 ccs;
//Adafruit_seesaw soilSensor;
DFRobot_SHT20 sht20;
OneWire oneWire(ONE_WIRE_BUS);
DallasTemperature sensors(&oneWire);
//PID myPID(&currentTemp, &PIDOut, &setPoint, Kp, Ki, Kd, DIRECT);

void setup() 
{
  //pinMode(HEATCABLE, OUTPUT);
  //myPID.SetMode(AUTOMATIC);
  
  initSHT20();
  initCCS811();
  //initSoil(); //Remettre avant serial.begin apr's avoir mis dans un try except les init
  
  Serial.begin(9600);
}

void loop()
{
  if(currentTime-pastTime >= UPDATE_DELAY_MS)
  {
    //readCableTemp();
    readCCS();
    readSHT20();
    readDS18B20();
    //readSoil();
    sendTrame();
    pastTime = currentTime;
  }
  currentTime = millis();
  delay(69);
  //setPIDOutput();
}

void initCCS811()
{
  if(!ccs.begin())
  {
    Serial.println("Failed to start sensor! Please check your wiring.");
    delay(1000);
  }
  // Wait for the sensor to be ready
  while(!ccs.available());
}

void initSHT20()
{
  sht20.initSHT20();                                  // Init SHT20 Sensor
  delay(100);
  sht20.checkSHT20();                                 // Check SHT20 Sensor
}

/*void initSoil()
{
  if (!soilSensor.begin(0x36)) 
  {
    Serial.println("ERROR! seesaw not found");
    while(1);
  } 
  else 
  {
    Serial.print("seesaw started! version: ");
    Serial.println(soilSensor.getVersion());
  }
}

void readSoil()
{
  uint16_t capread = soilSensor.touchRead(0);
  temp_GND = soilSensor.getTemp();
  humid_GND = mapFloatToPercent(capread,200,2000);
}*/
/*
void readCableTemp()
{
  sensors.requestTemperatures(); // Send the command to get temperature readings 
  currentTemp = sensors.getTempCByIndex(0);
}
*/


void readDS18B20()
{
  sensors.requestTemperatures(); // Send the command to get temperature readings
  tempDS = sensors.getTempCByIndex(0);
}

void readCCS()
{
  if(ccs.available())
  {
    if(!ccs.readData())
    {
      ppm_Dioxide = ccs.geteCO2();
      ppb_TVOC = ccs.getTVOC();
    }
    else
    {
      Serial.println("ERROR!");
      delay(1000);
    }
  }
}

void readSHT20()
{
  humid_SEN = sht20.readHumidity();                  // Read Humidity
  temp_SEN = sht20.readTemperature();               // Read Temperature
}

/*void setPIDOutput()
{
  myPID.Compute();
  if(PIDOut>40)
  {
    PIDOut=100;
    state_PID = HEATING;
  }
  else if(PIDOut <= 40 && PIDOut >0)
    state_PID = MAINTAIN;
  else
    state_PID = OFF;
    
  analogWrite(HEATCABLE, map(PIDOut,0,100,0,255));
}
*/
void sendTrame()
{
  String trame = String(temp_SEN)+";"+String(humid_SEN)+";"+String(ppm_Dioxide)+";"+String(ppb_TVOC)+";"+String(tempDS);
  Serial.println(trame);
}

/*float mapFloatToPercent(float var, float inLow, float inHigh)
{
  float ret = (((var-inLow)/(inHigh-inLow))*100);
  return ret;
}*/

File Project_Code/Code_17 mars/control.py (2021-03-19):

# -*- coding: utf-8 -*-

# Form implementation generated from reading ui file 'control.ui'
#
# Created by: PyQt5 UI code generator 5.14.1
#
# WARNING! All changes made in this file will be lost!

# Programme permettant d'afficher la fenêtre de changement de consigne. Cette fenêtre est ouverte par le programme MainGUI.py.
# Lorsque cette fenêtre est construite, elle reçoit la consigne courante et la limite de la consigne.
# Envoie la nouvelle consigne créé par Signal vers MainGUI.py

from PyQt5 import QtCore, QtGui, QtWidgets

# Classe pour l'objet Signal. Cette classe existe car si je déclarais mon signal è l'intérieur de Ui_Mainwindow1(), le Signal ne marchais pas.
class Calc(QtCore.QObject):
    submitted = QtCore.pyqtSignal(int) #Création de l'objet Signal
    def sendpls(self):   # Plus nécessaire au programme, je vais devoir l'enlever au prochain PUSH.
        print("send")
        self.submitted.emit("1")
        
# Création des objets graphiques de la fenêtre de controle.
class Ui_MainWindow1(object):
    def setup(self, MainWindow, controlTemp, limit):
        self.MainWindow = MainWindow
        
        self.limit = limit        
        self.control_Temp = controlTemp
        self.new_Temp = controlTemp
        
        self.MainWindow.setObjectName("MainWindow")
        self.MainWindow.resize(948, 650)
        self.centralwidget = QtWidgets.QWidget(MainWindow)
        self.centralwidget.setObjectName("centralwidget")
        self.gridLayout_2 = QtWidgets.QGridLayout(self.centralwidget)
        self.gridLayout_2.setObjectName("gridLayout_2")
        self.but_Val_down = QtWidgets.QPushButton(self.centralwidget)
        self.but_Val_down.setObjectName("but_Val_down")
        self.gridLayout_2.addWidget(self.but_Val_down, 0, 1, 1, 1)
        self.but_Cancel = QtWidgets.QPushButton(self.centralwidget)
        self.but_Cancel.setObjectName("but_Cancel")
        self.gridLayout_2.addWidget(self.but_Cancel, 2, 1, 1, 1)
        self.but_Val_up = QtWidgets.QPushButton(self.centralwidget)
        self.but_Val_up.setObjectName("but_Val_up")
        self.gridLayout_2.addWidget(self.but_Val_up, 0, 0, 1, 1)
        self.but_Submit = QtWidgets.QPushButton(self.centralwidget)
        self.but_Submit.setObjectName("but_Submit")
        self.gridLayout_2.addWidget(self.but_Submit, 2, 0, 1, 1)
        self.lcd_New = QtWidgets.QLCDNumber(self.centralwidget)
        self.lcd_New.setObjectName("lcd_New")
        self.gridLayout_2.addWidget(self.lcd_New, 1, 1, 1, 1)
        self.lcd_Current = QtWidgets.QLCDNumber(self.centralwidget)
        self.lcd_Current.setObjectName("lcd_Current")
        self.gridLayout_2.addWidget(self.lcd_Current, 1, 0, 1, 1)
        self.MainWindow.setCentralWidget(self.centralwidget)
        self.menubar = QtWidgets.QMenuBar(MainWindow)
        self.menubar.setGeometry(QtCore.QRect(0, 0, 948, 29))
        self.menubar.setObjectName("menubar")
        self.MainWindow.setMenuBar(self.menubar)
        self.statusbar = QtWidgets.QStatusBar(MainWindow)
        self.statusbar.setObjectName("statusbar")
        self.MainWindow.setStatusBar(self.statusbar)
        
        self.lcd_Current.display(self.control_Temp)  #affiche le set temp de temp courrant
        self.lcd_New.display(self.new_Temp)
        
        self.objsignal = Calc() #Création du Signal
        
        #Création des évênnement de fenêtre.
        self.but_Submit.clicked.connect(self.on_click_submit)
        self.but_Cancel.clicked.connect(self.on_click_Cancel)
        self.but_Val_up.clicked.connect(self.on_click_up)
        self.but_Val_down.clicked.connect(self.on_click_Down)
        
        self.retranslateUi()
        QtCore.QMetaObject.connectSlotsByName(self.MainWindow)

    def retranslateUi(self):
        _translate = QtCore.QCoreApplication.translate
        self.MainWindow.setWindowTitle(_translate("MainWindow", "MainWindow"))
        self.but_Val_down.setText(_translate("MainWindow", "DOWN"))
        self.but_Cancel.setText(_translate("MainWindow", "Cancel"))
        self.but_Val_up.setText(_translate("MainWindow", "UP"))
        self.but_Submit.setText(_translate("MainWindow", "Submit"))
    
    # Ferme la fenêtre control.py sans modifier les valeurs de consigne.
    def on_click_Cancel(self):
        self.MainWindow.close()
    
    # Ferme la fenêtre et envoie la nouvelle consigne par Signal vers MainGUI.py. 
    def on_click_submit(self):
        self.objsignal.submitted.emit(self.new_Temp) #Envoie de la valeur
        self.MainWindow.close() #ferme fenêtre
    
    # Augmente la valeur de 1
    def on_click_up(self):
        if(self.new_Temp < self.limit):
            self.new_Temp = self.new_Temp +1
            self.lcd_New.display(self.new_Temp)
            
    # Diminue la valeur de 1    
    def on_click_Down(self):
        if(self.new_Temp > 0):
            self.new_Temp = self.new_Temp -1
            self.lcd_New.display(self.new_Temp)

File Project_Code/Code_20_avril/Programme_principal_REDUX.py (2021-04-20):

#Programme_principal_REDUX.py

#  @file   Programme_principal_REDUX.py
#  @date   15 Fevrier 2021    
#  @author Simon Jourdenais
#  @brief  Programme principale du Raspberry Pi. Lecture de SEN0227, DS18B20 et lecture du port série.
#          La tramme recue contient les valeurs du CCS811. Les valeurs sont ensuites envoyées vers ThingSpeak
#          par URL(à chaque minute) et aussi envoyées au GUI MainGUI.py par MQTT sur le topic /test(+/- 2 secondes). Le programme écoute aussi le topic /test2. Lorsque le message reçoit la trame
#          contenant les consignes d'humiditées et les consignes de température, il "print" les deux valeurs. Ce programme montre que plusieurs parties du code finale sont terminées,
#          mais d'autres éléments vont y être ajoutés et ce code reste sujet a modification.
#  @material   Raspberry Pi 3 B, Arduino NANO, convertisseur 5V - 3.3V, Capteur CCS811, DS18B20, SEN0227

from time import time, sleep
import json
from urllib.request import urlopen
import sys
from signal import signal, SIGINT
import serial
import paho.mqtt.client as mqtt #import the client1
import paho.mqtt.publish as publish
from simple_pid import PID
import RPi.GPIO as GPIO
import classes


#WRITE_API = "OTSESYSMRPRYTJFL" # Clé a Simon
WRITE_API = "F6AG8QMUBNAO57IL"  # Clé à William
BASE_URL = "https://api.thingspeak.com/update?api_key={}".format(WRITE_API) #Déclaration de l'URL sur lequel notre programme va communiqué avec ThingSpeak.
 
'''cont_temp = 0   #Variable globale pour les consignes de température
cont_hum = 0     # Variable pour les consignes d'humidité'''

#GPIO.setmode(GPIO.BOARD)
#GPIO.setup(40, GPIO.OUT)

#soft_pwm = GPIO.PWM(40,500)
#soft_pwm.start(50)

#soft_pwm.stop()
#GPIO.cleanup()

#pid_HeatMat = PID(2,1,5, setpoint=30)
#pid_HeatMat.output_limits = (0, 255)

SensorPrevSec = 0  # Variable qui prend le temps de référence pour délais d'envoie MQTT
SensorInterval = 2 # 2 secondes de délais 
ThingSpeakPrevSec = 0 #Variable qui prend le temps référence pour délais d'envoie ThingSpeak
ThingSpeakInterval = 60 # 60 secondes de délais entre uploads



'''class c_Mesure:
    def __init__(self):
        self.tempRPI = -1
        self.co2 = -1
        self.tvoc = -1
        self.tempSEN = -1
        self.humSEN = -1
        self.tempDS = -1
        
    def updateValue(self, tup_Read):
            self.tempRPI = -1
            self.co2 = tup_Read[0]
            self.tvoc = tup_Read[1]
            self.tempSEN = tup_Read[2]
            self.humSEN = tup_Read[3]
            self.tempDS = tup_Read[4]'''
            
            
#class c_Control():
#    def __init__(self):
#        pass
    
#    def pidTemp(self):        
#        if(obj_mesure.tempDS != -1):
#            control = pid_HeatMat(obj_mesure.tempDS)

#            print(control)
#            controlcent = control*100/255
#            print(controlcent)
#            soft_pwm.ChangeDutyCycle(controlcent)
            
#        else:
#            print("TEMP CONTROL ERROR")

'''def pidTemp():
    
    if(obj_mesure.tempDS != -1):
        control = pid_HeatMat(obj_mesure.tempDS)

        print(control)
        controlcent = control*100/255
        print(controlcent)
        soft_pwm.ChangeDutyCycle(controlcent)
        
    else:
        print("TEMP CONTROL ERROR")'''


#Fonction qui lit le port série. Port de lecture /dev/serial0. Données de la provenance du ARDUINO NANO. Reçoit une string contenant deux valeurs.
#Première valeur CO2, deuxième TVOC.
'''def read_Serial():
    global ser
    ret_Val = (-1, -1, -1, -1, -1)  #Valeur mise par défault
    try:
        if ser.in_waiting > 0: 
            read_serial=ser.readline()   #lit ce qui a sur le port serie
            decoded_ser = read_serial.decode()  
            decoded_ser = decoded_ser.replace('\r\n', '')#enleve les saut de ligne
            data_CCS = decoded_ser.split(";")#sépare les valeurs du CO2 et de TOVC
            print(data_CCS[0]+" "+data_CCS[1]+" "+ data_CCS[2] +" "+ data_CCS[3]+" "+data_CCS[4])
            ret_Val = (int(data_CCS[2]), int(data_CCS[3]), float(data_CCS[0]), float(data_CCS[1]), float(data_CCS[4]))
            ser.flushInput() 
    except Exception as err:
        print(str(err))
        ser.close() #Ferme port série
    return ret_Val #Retourne les valeurs du capteur vers le main.'''

def handler(signal_received, frame):
    # Handle any cleanup here
    GPIO.cleanup()
    print('SIGINT or CTRL-C detected. Exiting gracefully')
    exit(0)


#Envoi les données vers ThingSpeak par URL. Contient: Température du DS18B20, Température et humidité du SEN0227, la concentartion de CO2 et le TVOC du CCS811.
#Données envoyées à la minute. ThingSpeak nous envoie le numéro de l'entré en retour si notre envoie c'est bien passé.
def save_To_Thingspeak(co2,tempDS,temp_Sol,humid_Sol, tvoc):
    try:
        thingspeakHttp = BASE_URL + "&field1={:.2f}&field2={:.1f}&field3={:.2f}&field4={:f}&field5={:f}".format(co2,tvoc,tempDS,temp_Sol,humid_Sol) #Fromattage de la string URL pour l'envoie vers ThingSpeak.
        print(thingspeakHttp)

        conn = urlopen(thingspeakHttp) #Envoie les infos vers ThingSpeak
        print("Response: {}".format(conn.read()))  #Reçoit réponse
        conn.close()

    except KeyboardInterrupt:
        conn.close()
    except Exception as err:
        print(str(err))
      
# Action lors de la connection au MQTT      
def on_connect(client, userdata, flags, rc):
    print("connected")  # Laisse savoir à l'usager qu'il est bien connecté

# Action à faire lorsqu'un message à été reçu sur /test2. 
def on_message(client, userdata, msg):
    #global cont_temp, cont_hum #Fait le lien avec les variables globales
    print(msg.payload.decode())
    try:
        incomingMQTT = msg.payload  #prend le message reçu
        incomingMQTT = json.loads(incomingMQTT) #Formatte le message sous format JSON
        
        obj_control.cont_temp = incomingMQTT["TEMP"]   #Constante Température changé
        obj_control.cont_hum = incomingMQTT["HUM"]   #Constante d'humidité changé
        print(obj_control.cont_temp)
        print(obj_control.cont_hum)
        obj_control.pid_HeatMat.setpoint = obj_control.cont_temp
    except Exception as err:
        print(err)

obj_mesure = classes.c_Mesure()
obj_control = classes.c_Control()
client = mqtt.Client("hell")   #Création du client MQTT
#Création des connections vers les fonctions des évênnements MQTT
client.on_connect = on_connect
client.on_message = on_message

client.connect("127.0.0.1") #connect to broker
client.subscribe("/test2")  #Écoute topic
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

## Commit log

2021-01-26 Creation du repos et ajout d'un script de test
2021-02-14 Ajout du code de test pour le capteur de CO2
2021-02-15 Modification de structure et push de tests unitaires
2021-02-16 Ajout du programme de lecture des 3 capteurs et d'ecriture influx
2021-03-15 Ajout de code du GUI avec le code de lecture
2021-03-16 Code Nano PID, Soil, SHT and CCS in one
2021-03-29 Ajout du Ui de la fenetre de controle
2021-03-29 ajout de mqttbuttontest3.ui a partir du nouveau pi
2021-03-29 Ajout de code plus a jour
2021-04-12 Fichier Kicad ajoutés
    [Mainblock_Connectors.sch, Mainblock_Core.sch, Mainblock_Power.sch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]
2021-04-30 GUI Added et Modif Kicad
    [Projet_ControlledEnvironment.kicad_pcb]
